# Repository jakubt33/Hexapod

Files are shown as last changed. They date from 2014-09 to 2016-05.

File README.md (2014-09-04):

Hexapod
=======

0b00 - Start communication in manual mode
0b01 - Start communication in auto mode
0b10 - Next bite
0b11 - End of message

Manual:
0b00|x x x x x x
0b10|L L L L L L 
0b10|L T T T T T
0b11|S S S S S P

Auto:
0b01|C C C C C c
0b11|c S S S S P

x - wchich leg is to be activated (1-6)
L - lift position
T - turn position
S - speed
P - power on(1)/power off(0)
c - command
C - Curve

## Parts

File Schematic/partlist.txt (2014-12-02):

Partlist

Exported from hexapod.brd at 2014-07-22 17:38:38

EAGLE Version 6.4.0 Copyright (c) 1988-2013 CadSoft

Assembly variant: 

Part     Value          Package       Library             Position (inch)       Orientation

BATTERY                 1X02          pinhead             (5.87 1.42)           R90
C1       100n           C0805K        rcl                 (2.52 2.8)            R90
C2       10n            C0805K        rcl                 (2.22 2.53)           R180
C3       100n           C0805K        rcl                 (3.12 2.89)           R270
C4       100n           C0805K        rcl                 (2.99 2.28)           R180
C5       1u             E2,5-5        rcl                 (2.25 2.29)           R270
C6       4.7uF          E2,5-5        rcl                 (3.42 2.9)            R270
C7       10p            C0805K        rcl                 (2.48 3.01)           R90
C8       10p            C0805K        rcl                 (1.98 2.71)           R180
C9       100n           C0805K        rcl                 (2.2 2.71)            R0
C10      100n           C0805K        rcl                 (4.05 2.87)           MR90
C11      47uF           E2,5-5        rcl                 (4.25 2.78)           R270
C12      47uF           E2,5-5        rcl                 (4.25 2.52)           R270
C13      100n           C0805K        rcl                 (4 2.54)              MR270
C14      100n           C0805K        rcl                 (4.16 2.02)           R90
C15      47uF           E2,5-5        rcl                 (3.47 2.14)           R90
C16      100n           C0805K        rcl                 (3.64 2.14)           MR90
DC                      733980-62     con-conrad          (5.79 2.28)           R90
F3       2A             SH22,5        fuse                (4.57 2.39)           R90
IC1      STM32F10XCXT6  TQFP48        stm32               (2.75 2.55)           R270
IC2      LM1117S(3.3)   SOT223        v-reg               (3.92 2.23)           MR0
IC4      LM1117S(5)     SOT223        v-reg               (3.78 2.7)            MR180
LED3V    Green          CHIP-LED0805  led                 (3.74 1.43)           R270
LED5V    Green          CHIP-LED0805  led                 (4.16 1.44)           R270
LED_BAT1 Green          CHIP-LED0805  led                 (3.71 2.36)           R270
LED_BAT2 Green          CHIP-LED0805  led                 (3.71 2.51)           R270
LED_BAT3 Green          CHIP-LED0805  led                 (3.71 2.66)           R270
LED_BAT4 Yellow         CHIP-LED0805  led                 (3.71 2.81)           R270
LED_BAT5 Red            CHIP-LED0805  led                 (3.71 2.96)           R270
LED_CONN blue           CHIP-LED0805  led                 (1.72 1.89)           R90
LED_LEG1 blue           CHIP-LED0805  led                 (1.22 1.28)           R0
LED_LEG2 blue           CHIP-LED0805  led                 (1.22 4.07)           R180
LED_LEG3 blue           CHIP-LED0805  led                 (2.53 1.27)           R0
LED_LEG4 blue           CHIP-LED0805  led                 (2.63 4.05)           R180
LED_LEG5 blue           CHIP-LED0805  led                 (4.8 1.24)            R0
LED_LEG6 blue           CHIP-LED0805  led                 (4.55 4.05)           R180
POT_ADC  5k             3223G         pot                 (3.79 2.07)           R90
Q1       24MHz          SM49          crystal             (2.16 2.88)           R0
Q2       SST5486        SOT23         transistor-fet      (2.48 1.91)           R0
Q3       SST5486        SOT23         transistor-fet      (2.49 3.27)           R180
Q4       SST5486        SOT23         transistor-fet      (2.27 3.27)           R180
Q5       SST5486        SOT23         transistor-fet      (2.91 1.92)           R0
Q6       SST5486        SOT23         transistor-fet      (3.11 1.92)           R0
Q7       SST5486        SOT23         transistor-fet      (3.31 1.92)           R0
Q8       SST5486        SOT23         transistor-fet      (3.32 3.27)           R180
Q14      SST5486        SOT23         transistor-fet      (2.26 1.91)           R0
Q15      SST5486        SOT23         transistor-fet      (2.7 1.92)            R0
Q17      SST5486        SOT23         transistor-fet      (3.12 3.27)           R180
Q18      SST5486        SOT23         transistor-fet      (2.92 3.27)           R180
Q19      SST5486        SOT23         transistor-fet      (2.71 3.27)           R180
R1       1k             M0805         resistor            (2.3 1.71)            R90
R2       1k             M0805         resistor            (2.52 1.71)           R90
R3       1k             M0805         resistor            (2.45 3.47)           R270
R4       1k             M0805         resistor            (2.23 3.47)           R270
R5       1k             M0805         resistor            (2.74 1.71)           R90
R6       1k             M0805         resistor            (3.08 3.47)           R270
R7       1k             M0805         resistor            (2.95 1.71)           R90
R8       1k             M0805         resistor            (3.15 1.71)           R90
R9       1k             M0805         resistor            (2.88 3.47)           R270
R10      1k             M0805         resistor            (2.67 3.47)           R270
R11      1k             M0805         resistor            (3.35 1.71)           R90
R12      1k             M0805         resistor            (3.28 3.48)           R270
R13      470            M0805         resistor            (3.92 2.36)           R0
R14      470            M0805         resistor            (3.92 2.51)           R0
R15      470            M0805         resistor            (3.92 2.66)           R0
R16      470            M0805         resistor            (3.92 2.81)           R0
R17      470            M0805         resistor            (3.92 2.96)           R0
R18      470            M0805         resistor            (1.22 1.49)           R90
R19      470            M0805         resistor            (1.22 3.85)           R270
R20      470            M0805         resistor            (2.49 1.41)           R180
R21      470            M0805         resistor            (2.63 3.87)           R270
R22      470            M0805         resistor            (4.8 1.44)            R90
R23      470            M0805         resistor            (4.55 3.86)           R90
R24      3K9            M0805         resistor            (3.92 2.23)           R0
R25      3k             M0805         resistor            (4.01 2.02)           R270
R26      10k            M0805         resistor            (4.1 3.55)            MR90
R27      10k            M0805         resistor            (3.81 3.71)           MR180
R28      10k            M0805         resistor            (4.2 3.55)            MR90
R29      10k            M0805         resistor            (3.81 3.19)           MR180
R30      10k            M0805         resistor            (3.65 3.09)           MR270
R31      10k            M0805         resistor            (3.81 3.32)           MR180
R32      10k            M0805         resistor            (3.81 3.58)           MR180
R33      10k            M0805         resistor            (3.81 3.45)           MR180
R34      470            M0805         resistor            (1.53 1.89)           R180
R35      470            M0805         resistor            (3.55 1.43)           R180
R36      820            M0805         resistor            (3.98 1.44)           R180
S3.3V    9077-2         9077-2        switch-misc         (3.64 1.68)           R0
S5       reset          SMS-001       smd-special         (2.01 2.29)           R0
S5V      9077-2         9077-2        switch-misc         (4.07 1.68)           R0
SKEYBT   9077-2         9077-2        switch-misc         (1.91 1.45)           R0
SR1                     MA03-1        con-lstb            (1.5 1.4)             R0
SR2                     MA03-1        con-lstb            (1.5 1.26)            R0
SR3                     MA03-1        con-lstb            (2.76 1.4)            R0
SR4                     MA03-1        con-lstb            (4.81 4.03)           R0
SR5                     MA03-1        con-lstb            (2.88 3.88)           R180
SR6                     MA03-1        con-lstb            (2.88 4.03)           R180
SR7                     MA03-1        con-lstb            (1.5 4.02)            R0
SR8                     MA03-1        con-lstb            (1.5 3.88)            R0
SR9                     MA03-1        con-lstb            (2.76 1.26)           R0
SR10                    MA03-1        con-lstb            (4.53 1.25)           R0
SR11                    MA03-1        con-lstb            (4.53 1.42)           R0
SR12                    MA03-1        con-lstb            (4.81 3.88)           R0
SV13                    ML20          con-harting-ml      (3.75 4.01)           R0
U$1      DEANS.MALE     DEANSM        bt_electromech      (5.37 1.3)            R270
U1       HC_06          BLUETOOTH_SMD SerialPortBluetooth (1.23 2.84)           R0
X1       DC             AK500/2       con-ptr500          (5.85 1.85)           R90

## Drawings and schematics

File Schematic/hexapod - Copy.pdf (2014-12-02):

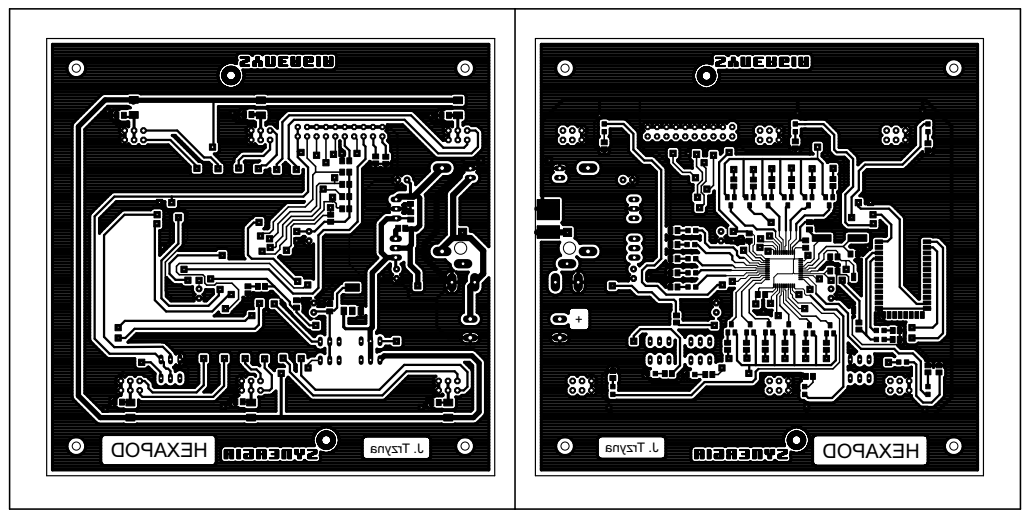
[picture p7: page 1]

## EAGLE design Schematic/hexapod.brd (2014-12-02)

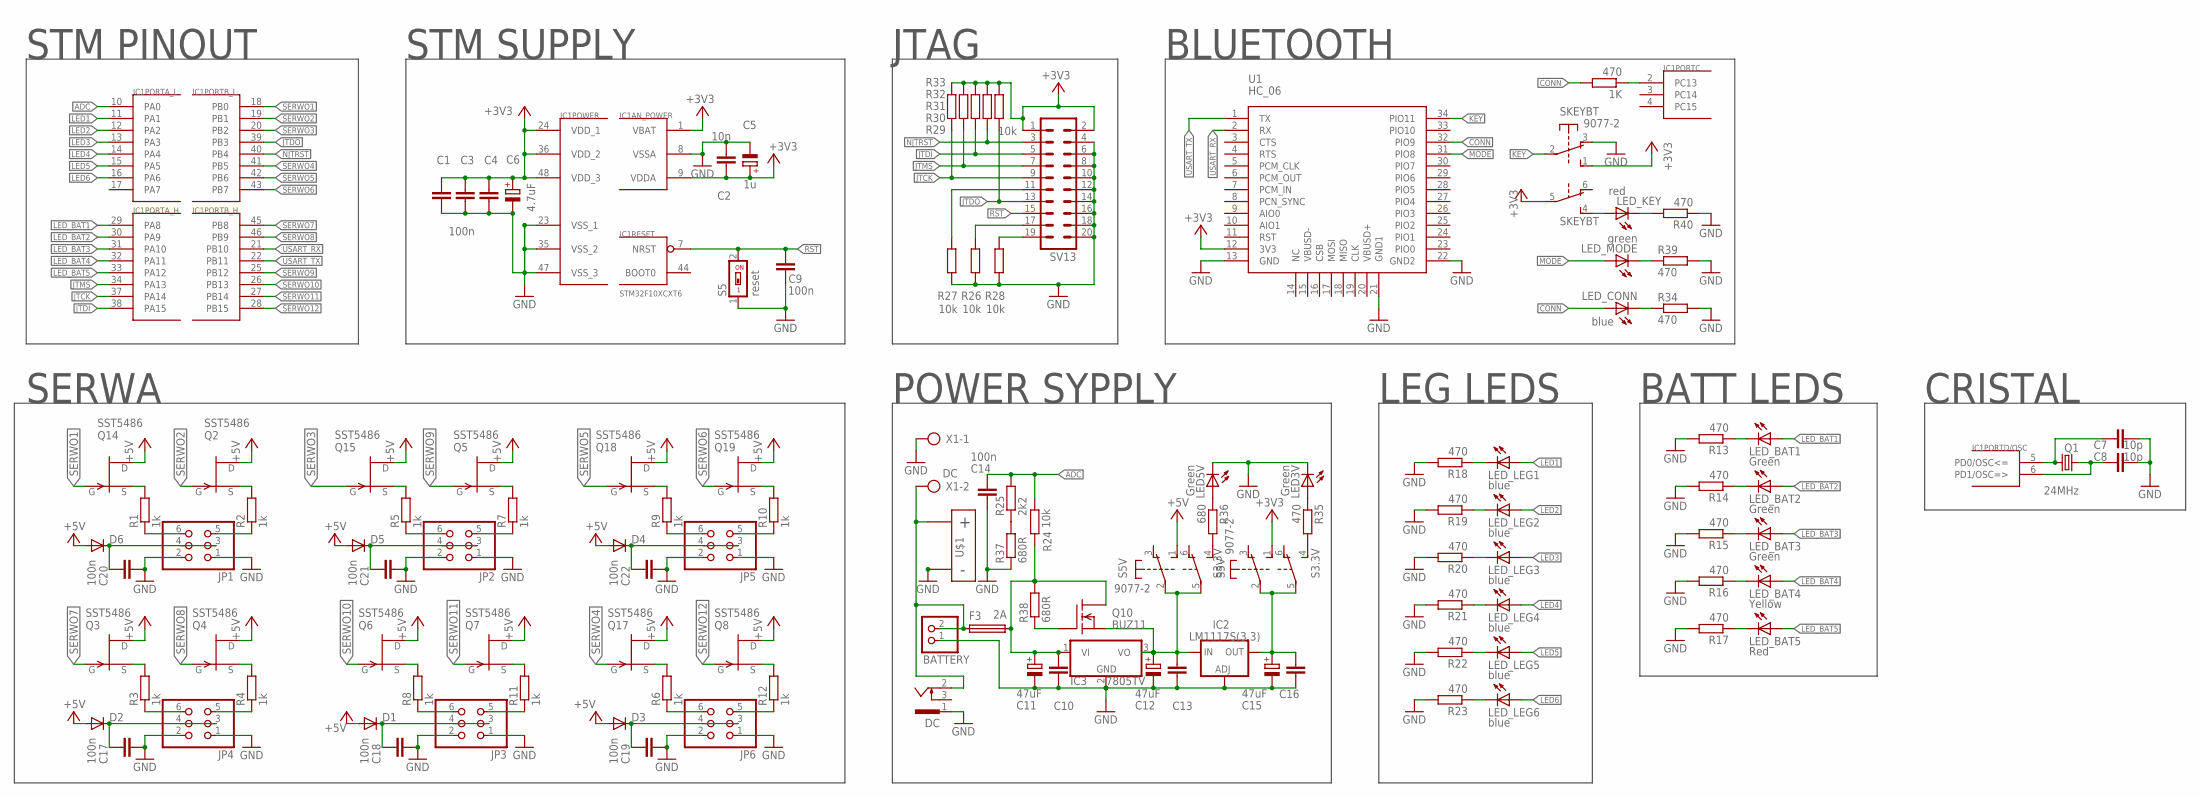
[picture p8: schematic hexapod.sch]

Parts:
1K: 470; M0805
BATTERY: PINHD-1X2; 1X02
C1, C3, C4, C9, C10, C13, C14, C16, C17, C18, C19, C20, C21, C22: 100n; C0805K
C2: 10n; C0805K
C5: 1u; E2,5-5
C6: 4.7uF; E2,5-5
C7, C8: 10p; C0805K
C11, C12, C15: 47uF; E2,5-5
D1, D2, D3, D4, D5, D6: DIODE-DO-214AC; DO-214AC
DC: 733980-62
F3: 2A; SH22,5
IC1: STM32F10XCXT6; TQFP48
IC2: LM1117S(3.3); SOT223
IC3: 7805TV; TO220V
JP1, JP2, JP3, JP4, JP5, JP6: PINHD-2X3; 2X03
LED3V, LED5V: Green; CHIP-LED0805
LED_BAT1, LED_BAT2, LED_BAT3: Green; CHIP-LED0805
LED_BAT4: Yellow; CHIP-LED0805
LED_BAT5: Red; CHIP-LED0805
LED_CONN: blue; CHIP-LED0805
LED_KEY: red; CHIP-LED0805
LED_LEG1, LED_LEG2, LED_LEG3, LED_LEG4, LED_LEG5, LED_LEG6: blue; CHIP-LED0805
LED_MODE: green; CHIP-LED0805
Q1: 24MHz; SM49
Q2, Q3, Q4, Q5, Q6, Q7, Q8, Q14, Q15, Q17, Q18, Q19: SST5486; SOT23
Q10: BUZ11; TO220
R1, R2, R3, R4, R5, R6, R7, R8, R9, R10, R11, R12: 1k; M0805
R13, R14, R15, R16, R17, R18, R19, R20, R21, R22, R23, R34, R35, R39, R40: 470; M0805
R24, R26, R27, R28, R29, R30, R31, R32, R33: 10k; M0805
R25: 2k2; M0805
R36: 680; M0805
R37, R38: 680R; M0805
S3.3V, S5V: 9077-2
S5: reset; SMS-001
SKEYBT: 9077-2
SV13: ML20
U1: HC_06; BLUETOOTH_SMD
U$1: DEANS.MALE; DEANSM
X1: DC; AK500/2

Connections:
+3V3: C1.1, C2.1, C3.1, C4.1, C5.+, C6.+, IC1.1 (VBAT), IC1.9 (VDDA), IC1.24 (VDD_1), IC1.36 (VDD_2), IC1.48 (VDD_3), R29.2, R30.2, R31.2, R32.2, R33.2, S3.3V.1 (S), SKEYBT.1 (S), SKEYBT.5, SV13.1, SV13.2, U1.12 (3V3)
+5V: D1.A, D2.A, D3.A, D4.A, D5.A, D6.A, Q2.1 (D), Q3.1 (D), Q4.1 (D), Q5.1 (D), Q6.1 (D), Q7.1 (D), Q8.1 (D), Q14.1 (D), Q15.1 (D), Q17.1 (D), Q18.1 (D), Q19.1 (D), S5V.1 (S)
ADC: C14.1, IC1.10 (PA0), R24.1, R25.2
CONN: 1K.2, LED_CONN.A, U1.32 (PIO9)
GND: BATTERY.1, C1.2, C2.2, C3.2, C4.2, C5.-, C6.-, C7.2, C8.2, C9.1, C10.2, C11.-, C12.-, C13.2, C14.2, C15.-, C16.2, C17.2, C18.2, C19.2, C20.2, C21.2, C22.2, DC.1, IC1.8 (VSSA), IC1.23 (VSS_1), IC1.35 (VSS_2), IC1.47 (VSS_3), IC2.1 (ADJ), IC3.2 (GND), JP1.1, JP1.2, JP2.1, JP2.2, JP3.1, JP3.2, JP4.1, JP4.2, JP5.1, JP5.2, JP6.1, JP6.2, LED3V.C, LED5V.C, R13.2, R14.2, R15.2, R16.2, R17.2, R18.2, R19.2, R20.2, R21.2, R22.2, R23.2, R26.1, R27.1, R28.1, R34.2, R37.1, R39.2, R40.1, S5.1, SKEYBT.3 (O), SV13.4, SV13.6, SV13.8, SV13.10, SV13.12, SV13.14, SV13.16, SV13.18, SV13.20, U1.13 (GND), U1.21 (GND1), U1.22 (GND2), U$1.P$NEG, X1.1
JTCK: IC1.37 (PA14), R29.1, SV13.9
JTDI: IC1.38 (PA15), R31.1, SV13.5
JTDO: IC1.39 (PB3), R33.1, SV13.13
JTMS: IC1.34 (PA13), R30.1, SV13.7
KEY: SKEYBT.2, U1.34 (PIO11)
LED1: IC1.11 (PA1), LED_LEG1.A
LED2: IC1.12 (PA2), LED_LEG2.A
LED3: IC1.13 (PA3), LED_LEG3.A
LED4: IC1.14 (PA4), LED_LEG4.A
LED5: IC1.15 (PA5), LED_LEG5.A
LED6: IC1.16 (PA6), LED_LEG6.A
LED_BAT1: IC1.29 (PA8), LED_BAT1.A
LED_BAT2: IC1.30 (PA9), LED_BAT2.A
LED_BAT3: IC1.31 (PA10), LED_BAT3.A
LED_BAT4: IC1.32 (PA11), LED_BAT4.A
LED_BAT5: IC1.33 (PA12), LED_BAT5.A
MODE: LED_MODE.A, U1.31 (PIO8)
unnamed: C7.1, IC1.5 (PD0/OSC<=), Q1.2
unnamed: C8.1, IC1.6 (PD1/OSC=>), Q1.1
unnamed: 1K.1, IC1.2 (PC13)
unnamed: Q14.2 (S), R1.2
unnamed: JP5.5, R10.1
unnamed: Q2.2 (S), R2.2
unnamed: JP3.5, R11.1
unnamed: JP5.6, R9.1
unnamed: JP3.6, R8.1
unnamed: R25.1, R37.2
unnamed: JP6.5, R12.1
unnamed: Q15.2 (S), R5.2
unnamed: JP2.5, R7.1
unnamed: Q18.2 (S), R9.2
unnamed: JP2.6, R5.1
unnamed: JP6.6, R6.1
unnamed: JP1.6, R1.1
unnamed: JP4.6, R3.1
unnamed: JP4.5, R4.1
unnamed: Q19.2 (S), R10.2
unnamed: JP1.5, R2.1
unnamed: R36.2, S5V.4 (S)
unnamed: C10.1, C11.+, F3.2, IC3.1 (VI), Q10.2 (D), R24.2, R38.2
unnamed: Q10.1 (G), R38.1
unnamed: LED_MODE.C, R39.1
unnamed: LED_KEY.A, SKEYBT.4 (S)
unnamed: LED_KEY.C, R40.2
unnamed: LED_BAT1.C, R13.1
unnamed: LED_LEG1.C, R18.1
unnamed: LED_BAT2.C, R14.1
unnamed: LED_LEG2.C, R19.1
unnamed: LED_BAT3.C, R15.1
unnamed: LED_LEG3.C, R20.1
unnamed: LED_BAT4.C, R16.1
unnamed: LED_LEG4.C, R21.1
unnamed: LED_BAT5.C, R17.1
unnamed: LED_LEG5.C, R22.1
unnamed: LED_LEG6.C, R23.1
unnamed: C18.1, D1.C, JP3.3, JP3.4
unnamed: LED_CONN.C, R34.1
unnamed: C15.+, C16.1, IC2.4 (OUT), S3.3V.2, S3.3V.5
unnamed: C12.+, C13.1, IC2.3 (IN), IC3.3 (VO), Q10.3 (S), S5V.2, S5V.5
unnamed: Q17.2 (S), R6.2
unnamed: R27.2, SV13.11
unnamed: Q3.2 (S), R3.2
unnamed: R35.2, S3.3V.4 (S)
unnamed: R26.2, SV13.17
unnamed: R28.2, SV13.19
unnamed: LED3V.A, R35.1
unnamed: C17.1, D2.C, JP4.3, JP4.4
unnamed: LED5V.A, R36.1
unnamed: BATTERY.2, DC.2, F3.1, U$1.P$POS, X1.2
unnamed: Q4.2 (S), R4.2
unnamed: Q5.2 (S), R7.2
unnamed: Q6.2 (S), R8.2
unnamed: Q7.2 (S), R11.2
unnamed: Q8.2 (S), R12.2
unnamed: C19.1, D3.C, JP6.3, JP6.4
unnamed: C22.1, D4.C, JP5.3, JP5.4
unnamed: C21.1, D5.C, JP2.3, JP2.4
unnamed: C20.1, D6.C, JP1.3, JP1.4
NJTRST: IC1.40 (PB4), R32.1, SV13.3
RST: C9.2, IC1.7 (NRST), S5.2, SV13.15
SERWO1: IC1.18 (PB0), Q14.3 (G)
SERWO2: IC1.19 (PB1), Q2.3 (G)
SERWO3: IC1.20 (PB2), Q15.3 (G)
SERWO4: IC1.41 (PB5), Q17.3 (G)
SERWO5: IC1.42 (PB6), Q18.3 (G)
SERWO6: IC1.43 (PB7), Q19.3 (G)
SERWO7: IC1.45 (PB8), Q3.3 (G)
SERWO8: IC1.46 (PB9), Q4.3 (G)
SERWO9: IC1.25 (PB12), Q5.3 (G)
SERWO10: IC1.26 (PB13), Q6.3 (G)
SERWO11: IC1.27 (PB14), Q7.3 (G)
SERWO12: IC1.28 (PB15), Q8.3 (G)
USART_RX: IC1.21 (PB10), U1.2 (RX)
USART_TX: IC1.22 (PB11), U1.1 (TX)

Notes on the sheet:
SERWA
BATT LEDS
LEG LEDS
POWER SYPPLY
JTAG
STM SUPPLY
CRISTAL
STM PINOUT
BLUETOOTH

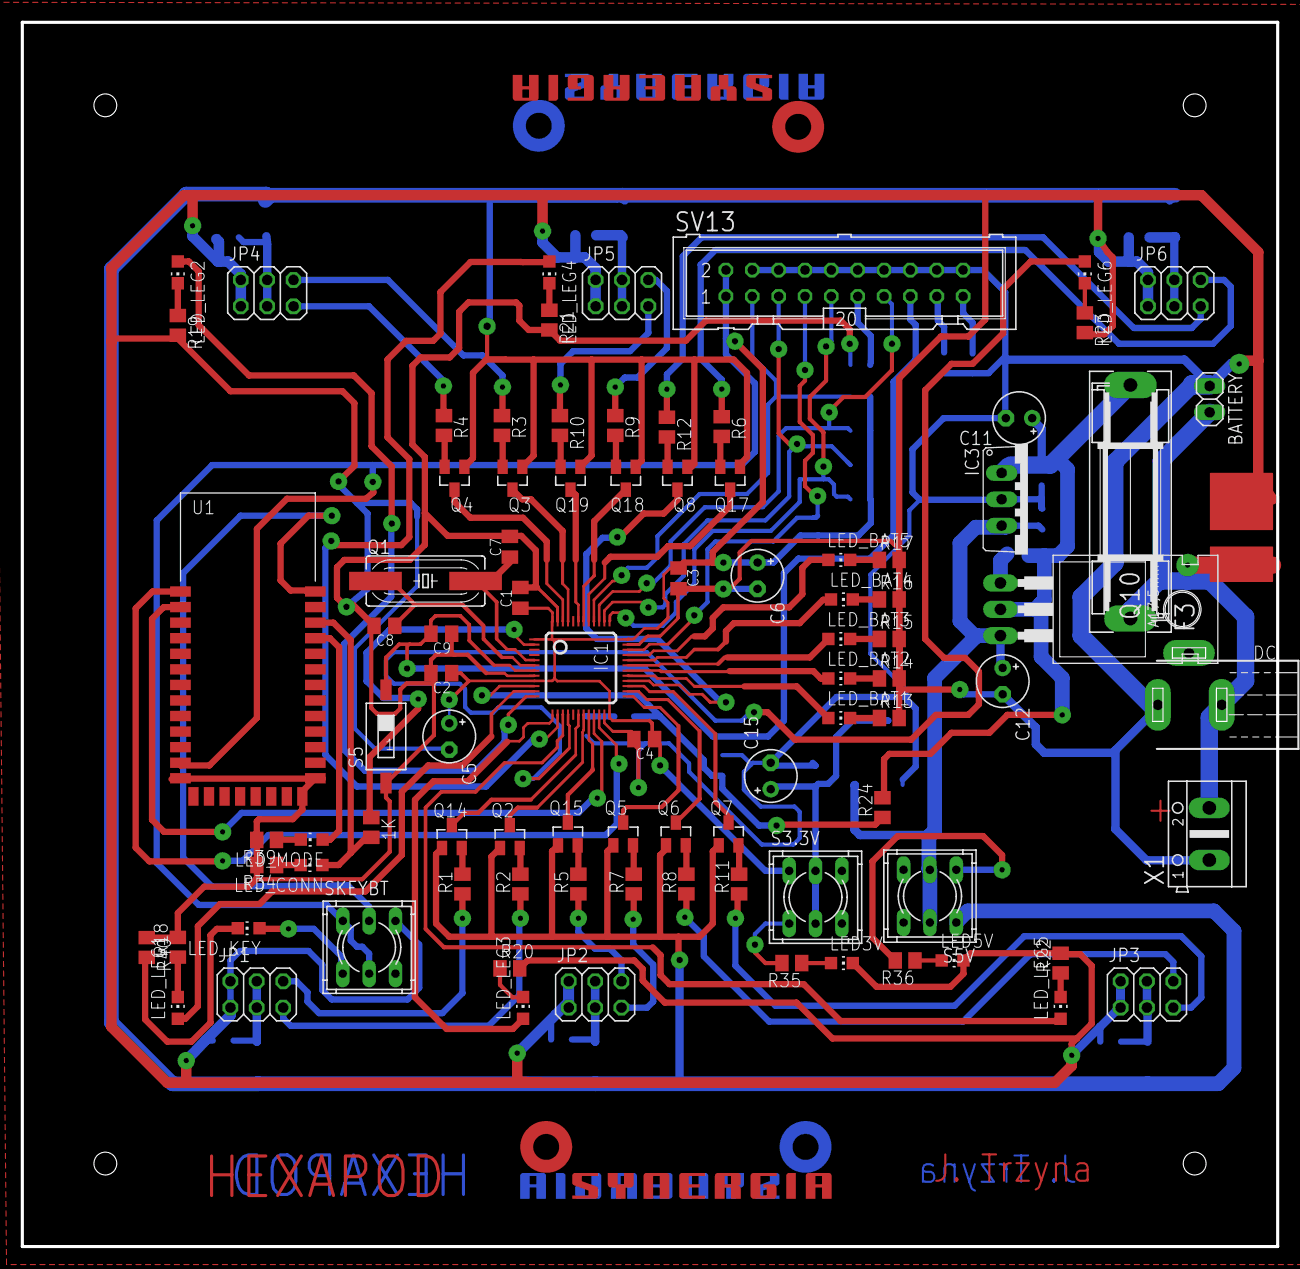
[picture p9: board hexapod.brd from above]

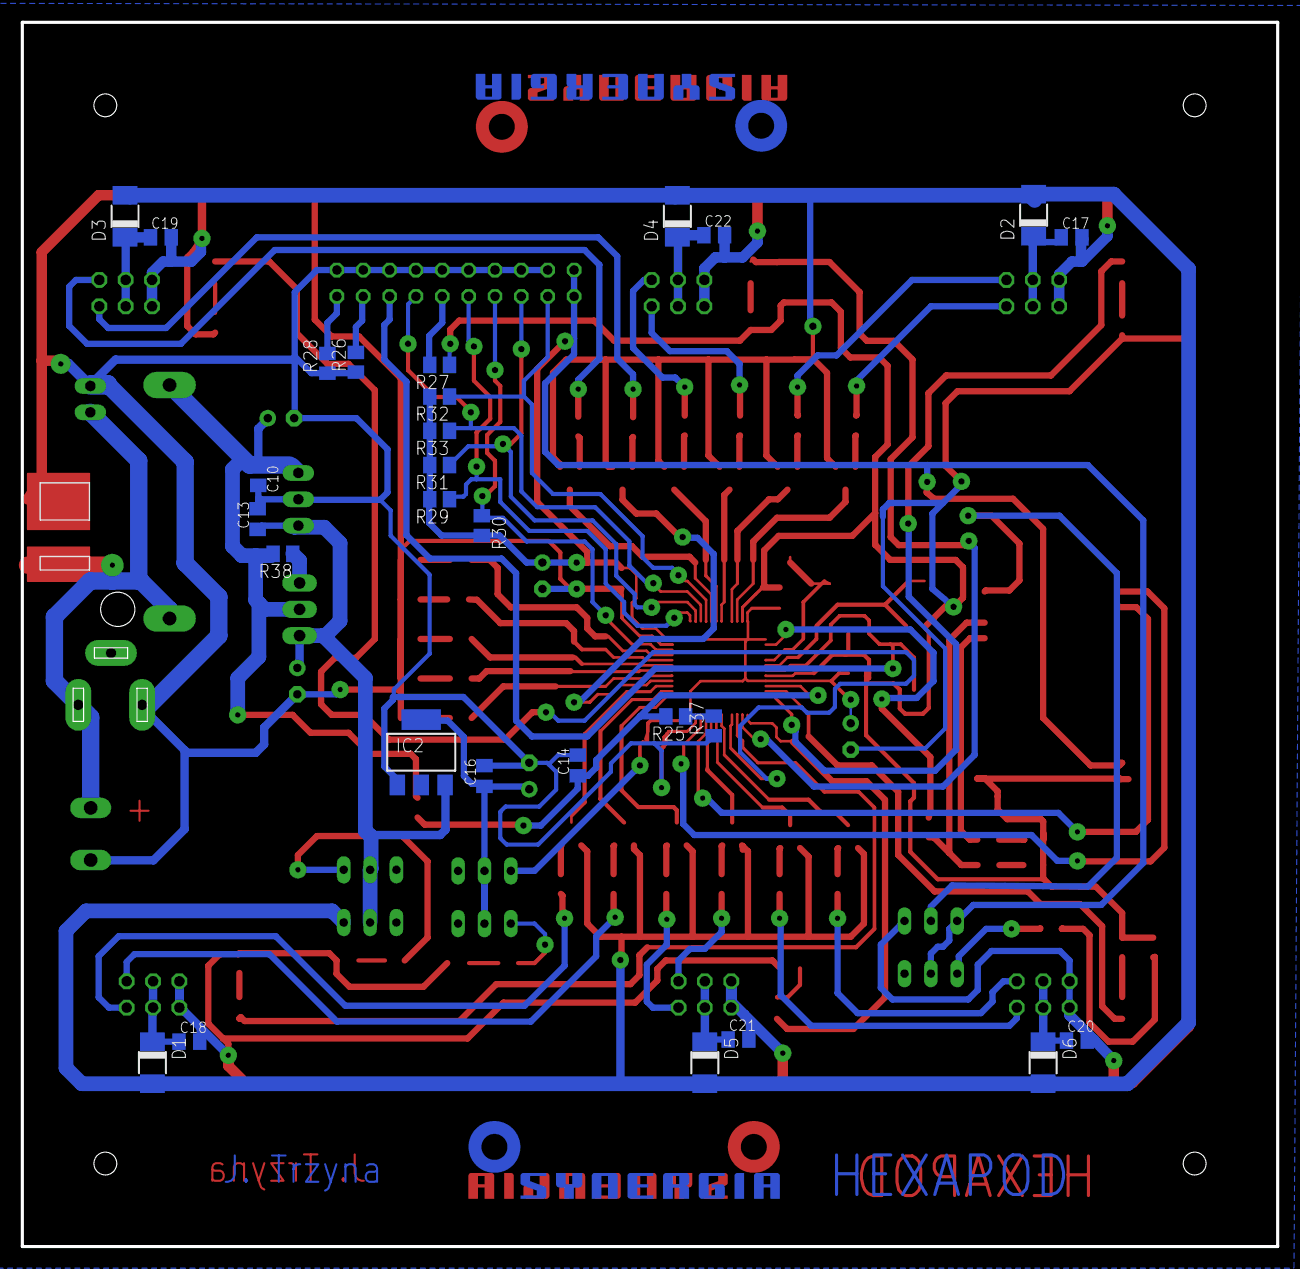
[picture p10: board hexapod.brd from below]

Board: 2 copper layers, 121.0 x 118.0 mm, 123 parts (30 on the bottom side), 99 nets.

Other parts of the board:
U$2, U$3, U$4, U$5: SYNERGIA_30MM

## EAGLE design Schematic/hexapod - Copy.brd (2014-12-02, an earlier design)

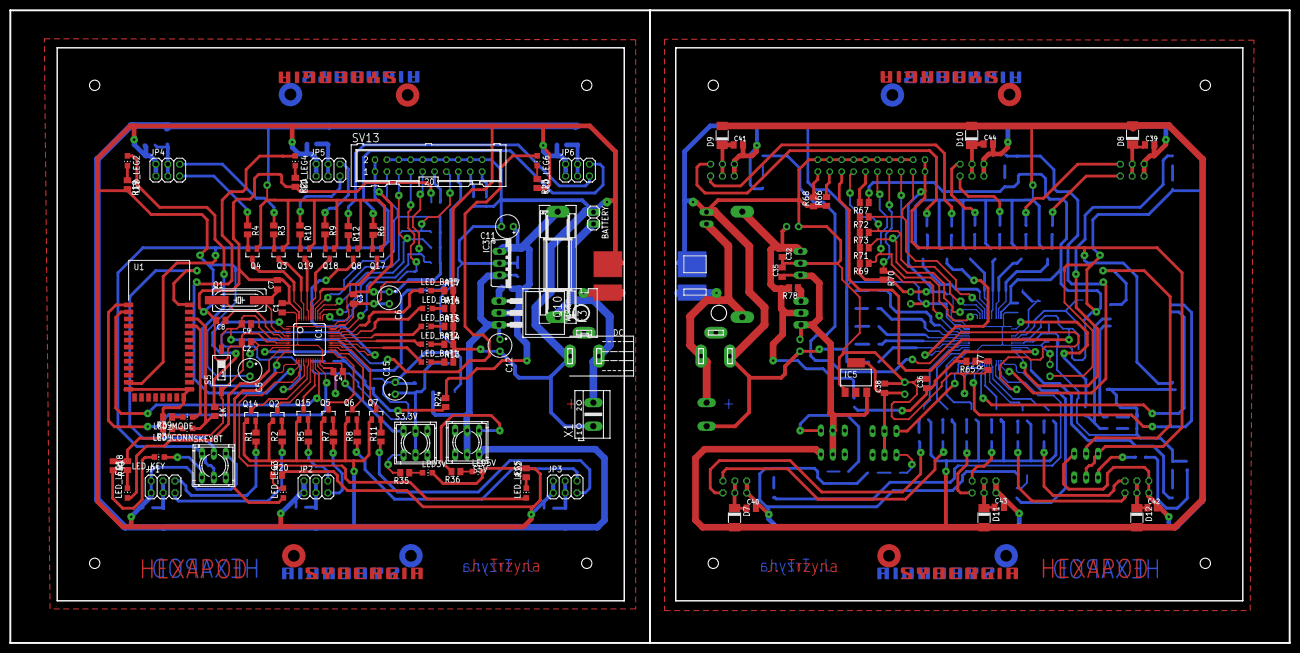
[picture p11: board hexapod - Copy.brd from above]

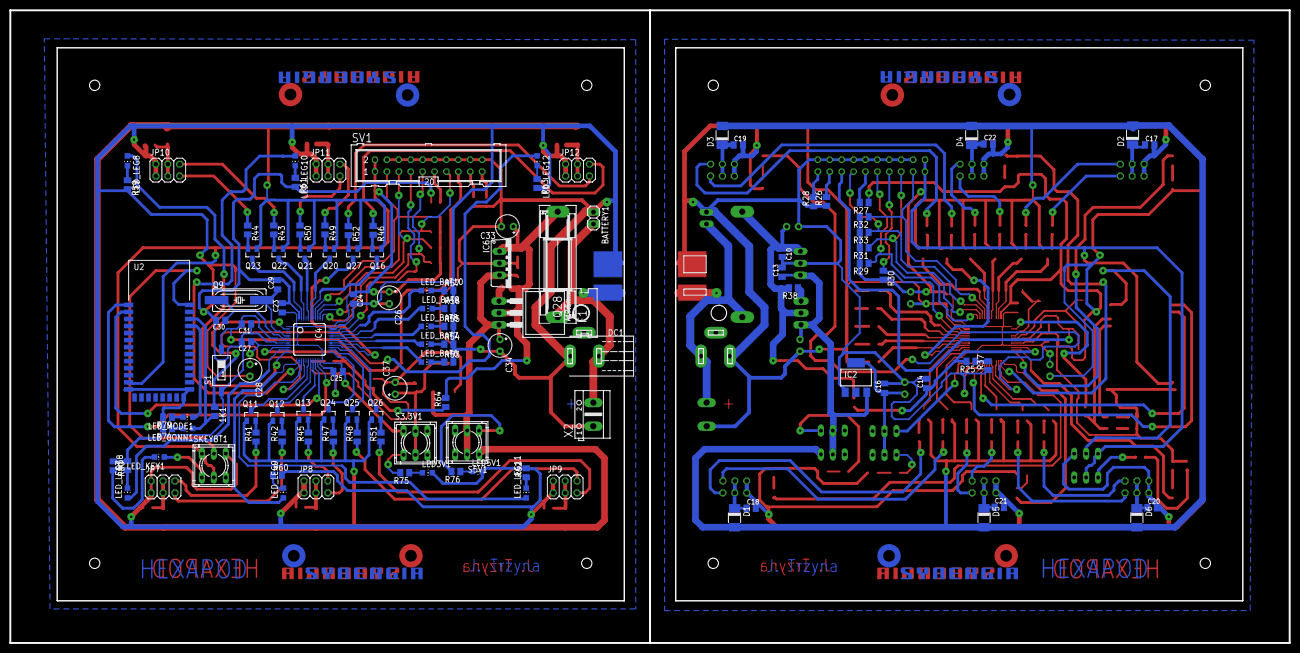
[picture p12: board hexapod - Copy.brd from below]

Board: 2 copper layers, 273.0 x 135.0 mm, 246 parts (123 on the bottom side), 198 nets.

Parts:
1K, 1K1: 470; M0805
BATTERY, BATTERY1: 1X02
C1, C3, C4, C9, C10, C13, C14, C16, C17, C18, C19, C20, C21, C22, C23, C24, C25, C31, C32, C35, C36, C38, C39, C40, C41, C42, C43, C44: 100n; C0805K
C2, C27: 10n; C0805K
C5, C28: 1u; E2,5-5
C6, C26: 4.7uF; E2,5-5
C7, C8, C29, C30: 10p; C0805K
C11, C12, C15, C33, C34, C37: 47uF; E2,5-5
D1, D2, D3, D4, D5, D6, D7, D8, D9, D10, D11, D12: DO-214AC
DC, DC1: 733980-62
F1, F3: 2A; SH22,5
IC1, IC4: STM32F10XCXT6; TQFP48
IC2, IC5: LM1117S(3.3); SOT223
IC3, IC6: 7805TV; TO220V
JP1, JP2, JP3, JP4, JP5, JP6, JP7, JP8, JP9, JP10, JP11, JP12: 2X03
LED3V, LED3V1, LED5V, LED5V1: Green; CHIP-LED0805
LED_BAT1, LED_BAT2, LED_BAT3, LED_BAT6, LED_BAT7, LED_BAT8: Green; CHIP-LED0805
LED_BAT4, LED_BAT9: Yellow; CHIP-LED0805
LED_BAT5, LED_BAT10: Red; CHIP-LED0805
LED_CONN, LED_CONN1: blue; CHIP-LED0805
LED_KEY, LED_KEY1: red; CHIP-LED0805
LED_LEG1, LED_LEG2, LED_LEG3, LED_LEG4, LED_LEG5, LED_LEG6, LED_LEG7, LED_LEG8, LED_LEG9, LED_LEG10, LED_LEG11, LED_LEG12: blue; CHIP-LED0805
LED_MODE, LED_MODE1: green; CHIP-LED0805
Q1, Q9: 24MHz; SM49
Q2, Q3, Q4, Q5, Q6, Q7, Q8, Q11, Q12, Q13, Q14, Q15, Q16, Q17, Q18, Q19, Q20, Q21, Q22, Q23, Q24, Q25, Q26, Q27: SST5486; SOT23
Q10, Q28: BUZ11; TO220
R1, R2, R3, R4, R5, R6, R7, R8, R9, R10, R11, R12, R41, R42, R43, R44, R45, R46, R47, R48, R49, R50, R51, R52: 1k; M0805
R13, R14, R15, R16, R17, R18, R19, R20, R21, R22, R23, R34, R35, R39, R40, R53, R54, R55, R56, R57, R58, R59, R60, R61, R62, R63, R74, R75, R79, R80: 470; M0805
R24, R64: 3K9; M0805
R25, R65: 2k2; M0805
R26, R27, R28, R29, R30, R31, R32, R33, R66, R67, R68, R69, R70, R71, R72, R73: 10k; M0805
R36, R76: 680; M0805
R37, R38, R77, R78: 680R; M0805
S1, S5: reset; SMS-001
S3.3V, S3.3V1, S5V, S5V1: 9077-2
SKEYBT, SKEYBT1: 9077-2
SV1, SV13: ML20
U1, U2: HC_06; BLUETOOTH_SMD
U$1, U$6: DEANS.MALE; DEANSM
U$2, U$3, U$4, U$5, U$7, U$8, U$9, U$10: SYNERGIA_30MM
X1, X2: DC; AK500/2

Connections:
+3V1: C23.1, C24.1, C25.1, C26.+, C27.1, C28.+, IC4.1, IC4.9, IC4.24, IC4.36, IC4.48, R69.2, R70.2, R71.2, R72.2, R73.2, S3.3V1.1, SKEYBT1.1, SKEYBT1.5, SV1.1, SV1.2, U2.12
+3V3: C1.1, C2.1, C3.1, C4.1, C5.+, C6.+, IC1.1, IC1.9, IC1.24, IC1.36, IC1.48, R29.2, R30.2, R31.2, R32.2, R33.2, S3.3V.1, SKEYBT.1, SKEYBT.5, SV13.1, SV13.2, U1.12
+5V: D1.A, D2.A, D3.A, D4.A, D5.A, D6.A, Q2.1, Q3.1, Q4.1, Q5.1, Q6.1, Q7.1, Q8.1, Q14.1, Q15.1, Q17.1, Q18.1, Q19.1, S5V.1
+5V1: D7.A, D8.A, D9.A, D10.A, D11.A, D12.A, Q11.1, Q12.1, Q13.1, Q16.1, Q20.1, Q21.1, Q22.1, Q23.1, Q24.1, Q25.1, Q26.1, Q27.1, S5V1.1
ADC: C14.1, IC1.10, R24.1, R25.2
ADC1: C36.1, IC4.10, R64.1, R65.2
CONN: 1K.2, LED_CONN.A, U1.32
CONN1: 1K1.2, LED_CONN1.A, U2.32
GND: BATTERY.1, C1.2, C2.2, C3.2, C4.2, C5.-, C6.-, C7.2, C8.2, C9.1, C10.2, C11.-, C12.-, C13.2, C14.2, C15.-, C16.2, C17.2, C18.2, C19.2, C20.2, C21.2, C22.2, DC.1, IC1.8, IC1.23, IC1.35, IC1.47, IC2.1, IC3.2, JP1.1, JP1.2, JP2.1, JP2.2, JP3.1, JP3.2, JP4.1, JP4.2, JP5.1, JP5.2, JP6.1, JP6.2, LED3V.C, LED5V.C, R13.2, R14.2, R15.2, R16.2, R17.2, R18.2, R19.2, R20.2, R21.2, R22.2, R23.2, R26.1, R27.1, R28.1, R34.2, R37.1, R39.2, R40.1, S5.1, SKEYBT.3, SV13.4, SV13.6, SV13.8, SV13.10, SV13.12, SV13.14, SV13.16, SV13.18, SV13.20, U1.13, U1.21, U1.22, U$1.P$NEG, X1.1
GND1: BATTERY1.1, C23.2, C24.2, C25.2, C26.-, C27.2, C28.-, C29.2, C30.2, C31.1, C32.2, C33.-, C34.-, C35.2, C36.2, C37.-, C38.2, C39.2, C40.2, C41.2, C42.2, C43.2, C44.2, DC1.1, IC4.8, IC4.23, IC4.35, IC4.47, IC5.1, IC6.2, JP7.1, JP7.2, JP8.1, JP8.2, JP9.1, JP9.2, JP10.1, JP10.2, JP11.1, JP11.2, JP12.1, JP12.2, LED3V1.C, LED5V1.C, R53.2, R54.2, R55.2, R56.2, R57.2, R58.2, R59.2, R60.2, R61.2, R62.2, R63.2, R66.1, R67.1, R68.1, R74.2, R77.1, R79.2, R80.1, S1.1, SKEYBT1.3, SV1.4, SV1.6, SV1.8, SV1.10, SV1.12, SV1.14, SV1.16, SV1.18, SV1.20, U2.13, U2.21, U2.22, U$6.P$NEG, X2.1
JTCK: IC1.37, R29.1, SV13.9
JTCK1: IC4.37, R69.1, SV1.9
JTDI: IC1.38, R31.1, SV13.5
JTDI1: IC4.38, R71.1, SV1.5
JTDO: IC1.39, R33.1, SV13.13
JTDO1: IC4.39, R73.1, SV1.13
JTMS: IC1.34, R30.1, SV13.7
JTMS1: IC4.34, R70.1, SV1.7
KEY: SKEYBT.2, U1.34
KEY1: SKEYBT1.2, U2.34
LED1: IC1.11, LED_LEG1.A
LED2: IC1.12, LED_LEG2.A
LED3: IC1.13, LED_LEG3.A
LED4: IC1.14, LED_LEG4.A
LED5: IC1.15, LED_LEG5.A
LED6: IC1.16, LED_LEG6.A
LED7: IC4.11, LED_LEG7.A
LED8: IC4.12, LED_LEG8.A
LED9: IC4.13, LED_LEG9.A
LED10: IC4.14, LED_LEG10.A
LED11: IC4.15, LED_LEG11.A
LED12: IC4.16, LED_LEG12.A
LED_BAT1: IC1.29, LED_BAT1.A
LED_BAT2: IC1.30, LED_BAT2.A
LED_BAT3: IC1.31, LED_BAT3.A
LED_BAT4: IC1.32, LED_BAT4.A
LED_BAT5: IC1.33, LED_BAT5.A
LED_BAT6: IC4.29, LED_BAT6.A
LED_BAT7: IC4.30, LED_BAT7.A
LED_BAT8: IC4.31, LED_BAT8.A
LED_BAT9: IC4.32, LED_BAT9.A
LED_BAT10: IC4.33, LED_BAT10.A
MODE: LED_MODE.A, U1.31
MODE1: LED_MODE1.A, U2.31
unnamed: C7.1, IC1.5, Q1.2
unnamed: C8.1, IC1.6, Q1.1
unnamed: 1K.1, IC1.2
unnamed: Q14.2, R1.2
unnamed: JP5.5, R10.1
unnamed: Q2.2, R2.2
unnamed: JP3.5, R11.1
unnamed: JP5.6, R9.1
unnamed: JP3.6, R8.1
unnamed: R25.1, R37.2
unnamed: JP6.5, R12.1
unnamed: Q15.2, R5.2
unnamed: JP2.5, R7.1
unnamed: Q18.2, R9.2
unnamed: JP2.6, R5.1
unnamed: JP6.6, R6.1
unnamed: JP1.6, R1.1
unnamed: JP4.6, R3.1
unnamed: JP4.5, R4.1
unnamed: Q19.2, R10.2
unnamed: JP1.5, R2.1
unnamed: R36.2, S5V.4
unnamed: C10.1, C11.+, F3.2, IC3.1, Q10.2, R24.2, R38.2
unnamed: Q10.1, R38.1
unnamed: LED_MODE.C, R39.1
unnamed: LED_KEY.A, SKEYBT.4
unnamed: LED_KEY.C, R40.2
unnamed: LED_BAT1.C, R13.1
unnamed: LED_LEG1.C, R18.1
unnamed: LED_BAT2.C, R14.1
unnamed: LED_LEG2.C, R19.1
unnamed: LED_BAT3.C, R15.1
unnamed: LED_LEG3.C, R20.1
unnamed: LED_BAT4.C, R16.1
unnamed: LED_LEG4.C, R21.1
unnamed: LED_BAT5.C, R17.1
unnamed: LED_LEG5.C, R22.1
unnamed: LED_LEG6.C, R23.1
unnamed: C18.1, D1.C, JP3.3, JP3.4
unnamed: LED_CONN.C, R34.1
unnamed: C15.+, C16.1, IC2.4, S3.3V.2, S3.3V.5
unnamed: C12.+, C13.1, IC2.3, IC3.3, Q10.3, S5V.2, S5V.5
unnamed: Q17.2, R6.2
unnamed: R27.2, SV13.11
unnamed: Q3.2, R3.2
unnamed: R35.2, S3.3V.4
unnamed: R26.2, SV13.17
unnamed: R28.2, SV13.19
unnamed: LED3V.A, R35.1
unnamed: C17.1, D2.C, JP4.3, JP4.4
unnamed: LED5V.A, R36.1
unnamed: BATTERY.2, DC.2, F3.1, U$1.P$POS, X1.2
unnamed: Q4.2, R4.2
unnamed: Q5.2, R7.2
unnamed: Q6.2, R8.2
unnamed: Q7.2, R11.2
unnamed: Q8.2, R12.2
unnamed: C19.1, D3.C, JP6.3, JP6.4
unnamed: C22.1, D4.C, JP5.3, JP5.4
unnamed: C21.1, D5.C, JP2.3, JP2.4
unnamed: C20.1, D6.C, JP1.3, JP1.4
unnamed: C29.1, IC4.5, Q9.2
unnamed: C30.1, IC4.6, Q9.1
unnamed: Q11.2, R41.2
unnamed: LED_BAT6.C, R53.1
unnamed: LED_BAT7.C, R54.1
unnamed: LED_BAT8.C, R55.1
unnamed: LED_BAT9.C, R56.1
unnamed: LED_BAT10.C, R57.1
unnamed: LED_LEG7.C, R58.1
unnamed: LED_LEG8.C, R59.1
unnamed: LED_LEG9.C, R60.1
unnamed: LED_LEG10.C, R61.1
unnamed: LED_LEG11.C, R62.1
unnamed: LED_LEG12.C, R63.1
unnamed: R67.2, SV1.11
unnamed: R66.2, SV1.17
unnamed: R68.2, SV1.19
unnamed: LED_CONN1.C, R74.1
unnamed: C37.+, C38.1, IC5.4, S3.3V1.2, S3.3V1.5
unnamed: C34.+, C35.1, IC5.3, IC6.3, Q28.3, S5V1.2, S5V1.5
unnamed: R75.2, S3.3V1.4
unnamed: LED3V1.A, R75.1
unnamed: LED5V1.A, R76.1
unnamed: BATTERY1.2, DC1.2, F1.1, U$6.P$POS, X2.2
unnamed: Q12.2, R42.2
unnamed: Q13.2, R45.2
unnamed: Q16.2, R46.2
unnamed: Q20.2, R49.2
unnamed: Q21.2, R50.2
unnamed: Q22.2, R43.2
unnamed: Q23.2, R44.2
unnamed: Q24.2, R47.2
unnamed: Q25.2, R48.2
unnamed: Q26.2, R51.2
unnamed: Q27.2, R52.2
unnamed: R65.1, R77.2
unnamed: JP7.6, R41.1
unnamed: JP7.5, R42.1
unnamed: JP8.5, R47.1
unnamed: JP8.6, R45.1
unnamed: JP9.5, R51.1
unnamed: JP9.6, R48.1
unnamed: JP10.6, R43.1
unnamed: JP10.5, R44.1
unnamed: JP11.5, R50.1
unnamed: JP11.6, R49.1
unnamed: JP12.5, R52.1
unnamed: JP12.6, R46.1
unnamed: R76.2, S5V1.4
unnamed: C32.1, C33.+, F1.2, IC6.1, Q28.2, R64.2, R78.2
unnamed: Q28.1, R78.1
unnamed: 1K1.1, IC4.2
unnamed: LED_MODE1.C, R79.1
unnamed: LED_KEY1.A, SKEYBT1.4
unnamed: LED_KEY1.C, R80.2
unnamed: C40.1, D7.C, JP9.3, JP9.4
unnamed: C39.1, D8.C, JP10.3, JP10.4
unnamed: C41.1, D9.C, JP12.3, JP12.4
unnamed: C44.1, D10.C, JP11.3, JP11.4
unnamed: C43.1, D11.C, JP8.3, JP8.4
unnamed: C42.1, D12.C, JP7.3, JP7.4
NJTRST: IC1.40, R32.1, SV13.3
NJTRST1: IC4.40, R72.1, SV1.3
RST: C9.2, IC1.7, S5.2, SV13.15
RST1: C31.2, IC4.7, S1.2, SV1.15
SERWO1: IC1.18, Q14.3
SERWO2: IC1.19, Q2.3
SERWO3: IC1.20, Q15.3
SERWO4: IC1.41, Q17.3
SERWO5: IC1.42, Q18.3
SERWO6: IC1.43, Q19.3
SERWO7: IC1.45, Q3.3
SERWO8: IC1.46, Q4.3
SERWO9: IC1.25, Q5.3
SERWO10: IC1.26, Q6.3
SERWO11: IC1.27, Q7.3
SERWO12: IC1.28, Q8.3
SERWO13: IC4.18, Q11.3
SERWO14: IC4.19, Q12.3
SERWO15: IC4.20, Q13.3
SERWO16: IC4.41, Q16.3
SERWO17: IC4.42, Q20.3
SERWO18: IC4.43, Q21.3
SERWO19: IC4.45, Q22.3
SERWO20: IC4.46, Q23.3
SERWO21: IC4.25, Q24.3
SERWO22: IC4.26, Q25.3
SERWO23: IC4.27, Q26.3
SERWO24: IC4.28, Q27.3
USART_RX: IC1.21, U1.2
USART_RX1: IC4.21, U2.2
USART_TX: IC1.22, U1.1
USART_TX1: IC4.22, U2.1

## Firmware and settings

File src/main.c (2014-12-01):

#include "stm32f10x.h"
#include <stm32f10x_rcc.h>
#include <stm32f10x_gpio.h>
#include <system_stm32f10x.h>


#define FALSE 0
#define TRUE  1
#define DONE  1
#define ADC_MeanDivider 7 //64
#define ADC_MaxCounter 127

volatile int ConnectionEstablished = FALSE;
volatile u8 BatteryDischarged = FALSE;
volatile u8 PowerON = FALSE;
volatile u16 ADC_Mean = 0;
volatile u8 ADC_Counter = 0; //max 64->Div'6

void delay_ms(int LocalCounter);
void delay_us(int LocalCounter);

#include "leds.h"
#include "serwo.h"
#include "movement.h"
#include "bluetooth.h"
#include "init.h"

void checkBattery();

int main(void)
{
	init_Clock();
	init_LED();
	init_Servo();
	init_ADC();
	init_TIM2();
	init_Bluetooth();

	basePosition();
	while (1)
	{
		checkBattery();
		checkConnection();
		while(ConnectionEstablished == TRUE)
		{
			checkBattery();
			checkBluetooth();
			checkIfConnectionLost();
		}
	}

}

void checkBattery()
{
	volatile u8  ADC_value = (ADC1->DR) >> 4;

	if(ADC_Counter < ADC_MaxCounter)
	{
		ADC_Mean += ADC_value;
		ADC_Counter++;
		if(GPIO_ReadInputDataBit(BTPORT, CONNECTIONPIN) == RESET) //connection not
		{
			ADC_Counter = ADC_MaxCounter;
		}
	}
	if(ADC_Counter >= ADC_MaxCounter)
	{
		if(GPIO_ReadInputDataBit(BTPORT, CONNECTIONPIN) == SET) //if connection established
		{
			ADC_Mean = ADC_Mean >> ADC_MeanDivider;
		}


		if(ADC_Mean<Batt_critical_value)
			batt_critical();
		else if(ADC_Mean<Batt_1_5_value)
			batt_1_5();
		else if(ADC_Mean<Batt_2_5_value)
			batt_2_5();
		else if(ADC_Mean<Batt_3_5_value)
			batt_3_5();
		else if(ADC_Mean<Batt_4_5_value)
			batt_4_5();
		else
			batt_5_5();

		ADC_Counter = 0;
		ADC_Mean = 0;
	}

	//USART_SendData(USART3, ADC_value);

}

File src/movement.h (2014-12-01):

/*
 * movement.h
 *
 *  Created on: Aug 18, 2014
 *      Author: Jakub Trzyna
 */

#ifndef MOVEMENT_H_
#define MOVEMENT_H_


void basePosition()
{
	char Leg=0;

	for(Leg=0b00000001; Leg<=0b00100000; Leg*=2)
	{
		if( (legLift(Leg, 0, MAX_SPEED) != DONE) || (legTurn(Leg, 0, MAX_SPEED, 0, 1) != DONE) )
		{
			while( legLift(Leg, 13, 11) != DONE ); //(Leg, 38, 11)
			while( legTurn(Leg, 0, 11, 0, 1) != DONE );
			while( legLift(Leg, 0, 11) != DONE );
		}
	}

	Step = 0;
}

void layDown() //protocol must be changed to handle this function
{
	while( legTurn(0b111111, 0, 13, 0, 0) != DONE );
	while( legLift(0b111111, 20, 13) != DONE );

}

void curveAdjust(int *Curve) // 0 to 28
{
	*Curve -= 14;

	switch(*Curve)
	{
	case -14: {
		*Curve = -19;//-56;
		break;
	}
	case -13: {
		*Curve = -19;//-28;
		break;
	}
	case -12: {
		*Curve = -10;//-28;
		break;
	}
	case -11: {
		*Curve = -10; //-24;
		break;
	}
	case -10: {
		*Curve = -9; //-24;
		break;
	}
	case 10: {
		*Curve = 9; //-24;
		break;
	}
	case 11: {
		*Curve = 10;//24;
		break;
	}
	case 12: {
		*Curve = 10;//28;
		break;
	}
	case 13: {
		*Curve = 19;//28;
		break;
	}
	case 14: {
		*Curve = 19;//56;
		break;
	}
	default: {
		break;
	}
	}
}

void go(int Speed, int Curve, int Direction)
{
	if(Speed>14) Speed = 14;

	if( (Step < 11) || (Step > 16) ) //it means that different action was previously done
	{
		basePosition();
		Step = 11;
	}


	if(Step == 11) {
		if( legLift(0b101010, 12, Speed) == DONE ) //45
			Step = 12;
	}

	else if((Step == 12) && (Direction == 1) ) {
		if( legTurn(0b111111, -9, Speed, Curve, Direction) == DONE ) //-28
			Step = 13;
	}
	else if((Step == 12) && (Direction == 2) ) {
		if( legTurn(0b111111, 9, Speed, Curve, Direction) == DONE ) //28
			Step = 13;
	}

	else if(Step == 13) {
		if( legLift(0b101010, 3, Speed) == DONE ) //15
			Step = 14;
	}


	else if(Step == 14) {
		if(	legLift(0b010101, 12, Speed) == DONE ) //45
			Step = 15;
	}

	else if( (Step == 15) && (Direction == 1) ) { //45
		if(	legTurn(0b111111, 9, Speed, Curve, Direction) == DONE ) //28
			Step = 16;
	}
	else if( (Step == 15) && (Direction == 2) ) { //45
		if(	legTurn(0b111111, -9, Speed, Curve, Direction) == DONE ) //28
			Step = 16;
	}

	else if(Step == 16) {
		if( legLift(0b010101, 3, Speed) == DONE ) //15
			Step = 11;
	}
}

#endif /* MOVEMENT_H_ */

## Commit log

2014-08-01 Leds flashing
2014-08-01 adc activated, leds indicate battery level
2014-08-01 battery level indicator is much smarter, max voltage defined by user (12.6V)
2014-08-01 PWM set by software - 50hz with step size 1/90
2014-08-05 speed regulator
2014-08-14 flashing leds via BT, data coded in SSJP
    SSJP - super secure jakub's protocol
2014-08-14 manual mode: steering each leg works, speed regulation doesnt work as should
2014-08-17 rebuiling PWM, better optimalisation, LIFT calibration
    to do: the same with TURN, add functions to lift
2014-08-18 checking bluetooth connection
    check bluetooth receiver function, add sending battery level, rebuild
    labview program
2014-08-19 manual mode works as it should
    add auto mode, and battery indicator
2014-08-21 manual mode almost works, check selecting legs function
2014-08-21 selecting legs, lifting and turning fixed
    add more functionality! :dancers:
    [bluetooth.h, serwo.h]
2014-08-21 LabView shows battery level
    add setting battery voltage
2014-08-22 turning left and right
    without one servo it's hard to tell how much this function is efficient
2014-08-25 power button works, probably
2014-08-27 single leg selector, problem with monostable buttons eliminated
    [movement.h]
2014-08-28 basePosition(): speed readjusted, fixed value
    [movement.h]
2014-09-04 goAhead() with turning done,
    readjust turning, more speed would be great. Back:turning wrong side
    [bluetooth.h, movement.h, serwo.h]
2014-09-05 some fails, revert needed!
    [bluetooth.h, main.c, movement.h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]
2014-09-11 turning sensitivity adjusted, better optimalisation
    -PowerOff variable
    -battery resolution
2014-09-13 separete (manual and automatic) button to cut off the power
2014-09-13 max speed lag fixed
    [serwo.h]
2014-09-14 receiver (LV) lag fixed
    only half a second, acceptable result
    [bluetooth.h, main.c]
2014-09-14 battery indicator fixed
2014-09-14 smooth battery indicator (mean of 100 variables)
2014-09-14 manual mode: turning fixed
    [bluetooth.h, movement.h]
2014-09-14 Final v1.00. Pad: SingleLegMode - steering fixed
    [serwo.h]
2014-09-22 Android: list of paired devices
2014-09-22 Android: button: showPairedDevices
2014-09-25 discovering devices
2014-10-05 steeringWheel - onTouchEvent
2014-10-05 steeringWheel - center of coords system
2014-10-24 PWM slightly readjust to get 50Hz
2014-11-09 Labview Final V1.98
    stop button->connect to first loop
2014-11-20 downcloced to 24mhz, sending adc disabled
2014-11-20 leg 2 and 5 replaced (in order to have better balance)
    [serwo.h]
2014-11-22 oc to 32mhz,
    add: adc main value(stm), try to flush in ich iteration, and. app only
    in portrait mode + base posiotion button
2014-12-01 STM->mean, low battery protection
2014-12-02 schematic moved to git repo
    [DRILEGEND.CFG, hexapod - Copy.brd, hexapod.brd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]
2014-12-03 android: crash fixed (after clicking power on button)
2016-05-11 new steering wheel image, refreshed some themes
